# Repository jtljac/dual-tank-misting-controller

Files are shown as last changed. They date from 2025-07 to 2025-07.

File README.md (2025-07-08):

A circuit board design and ESPHome script for a control board responsible for a misting system for two tanks.  
A route from the pump to each tank can be enabled using solenoids attched to their labelled terminals. Powered terminals
will be indicated by an indicator LED, including when the pump is powered.

There are also a header for a Dallas 1-Wire DS18b20 waterproof temperature sensor for measuring the temperature of the 
water Tank, and a header for a HC-SR04 ultrasonic Distance sensor for use as a water level indicator. The HC-SR04 header
has an associate voltage selector header as they're supposed to be 5v but my cheap ones overheated above 3v3.

The board is powered using a 24V DC Barrel Jack and powers the pump and solenoids directly. This design has sized 
components and traces for 3A, which is generous for the required current for the ESP, pump, and two solenoids.

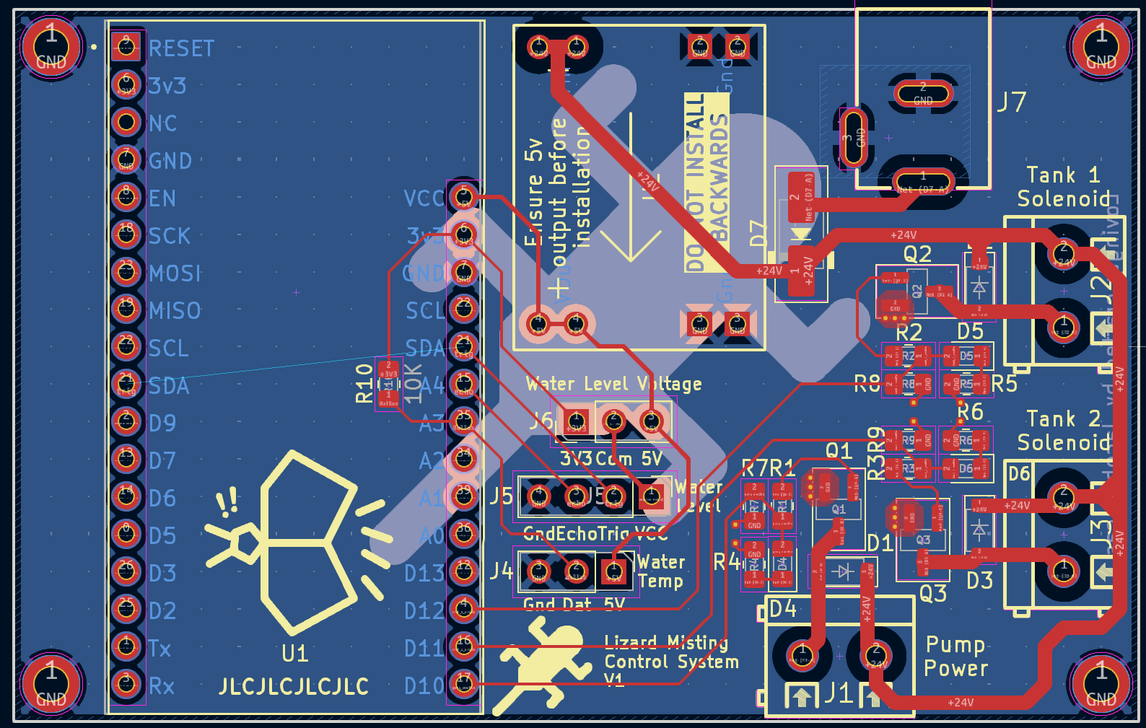
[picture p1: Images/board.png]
V1 Board


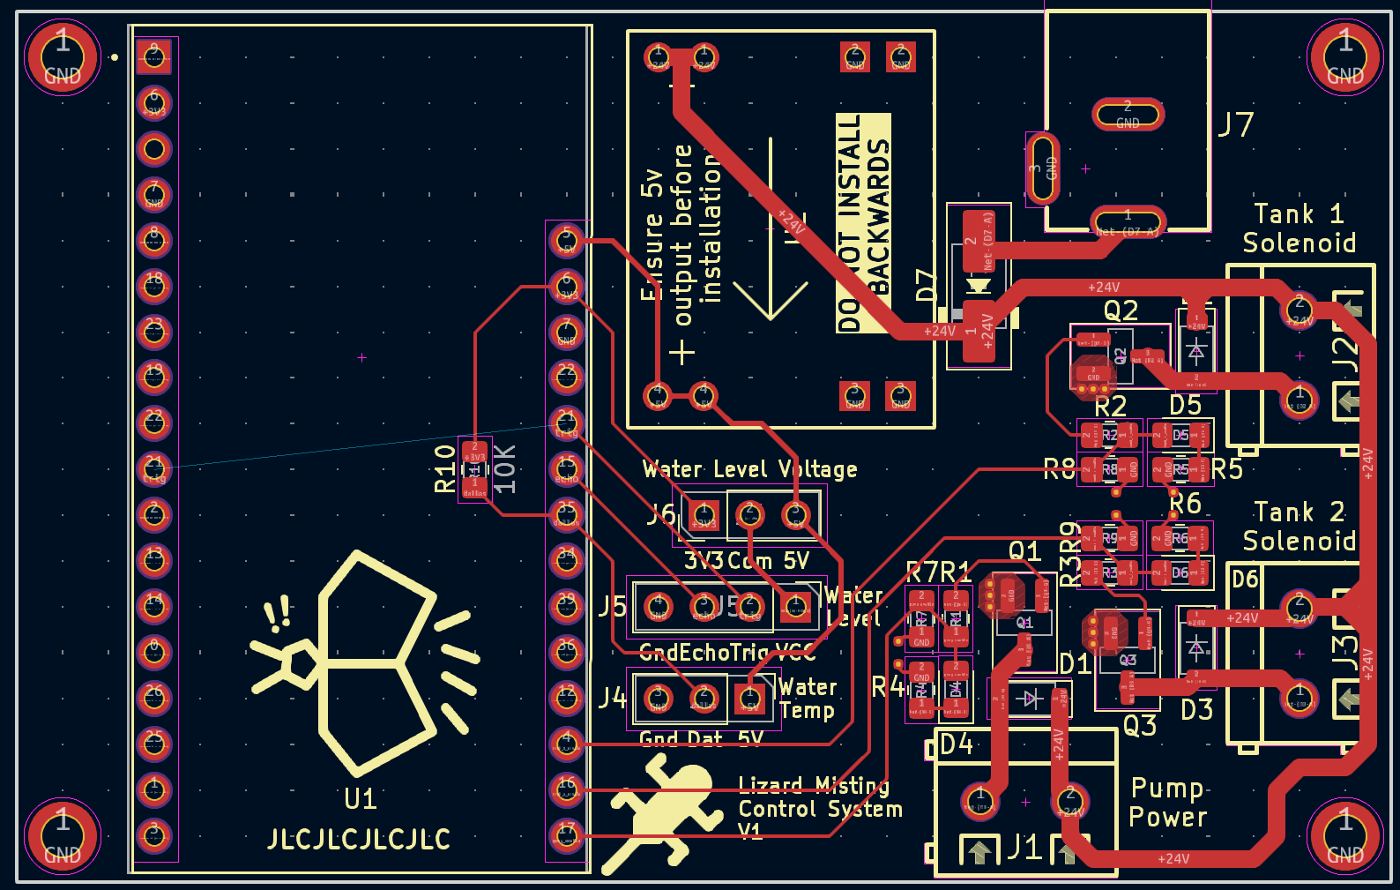
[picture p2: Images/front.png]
V1 Board Front Only


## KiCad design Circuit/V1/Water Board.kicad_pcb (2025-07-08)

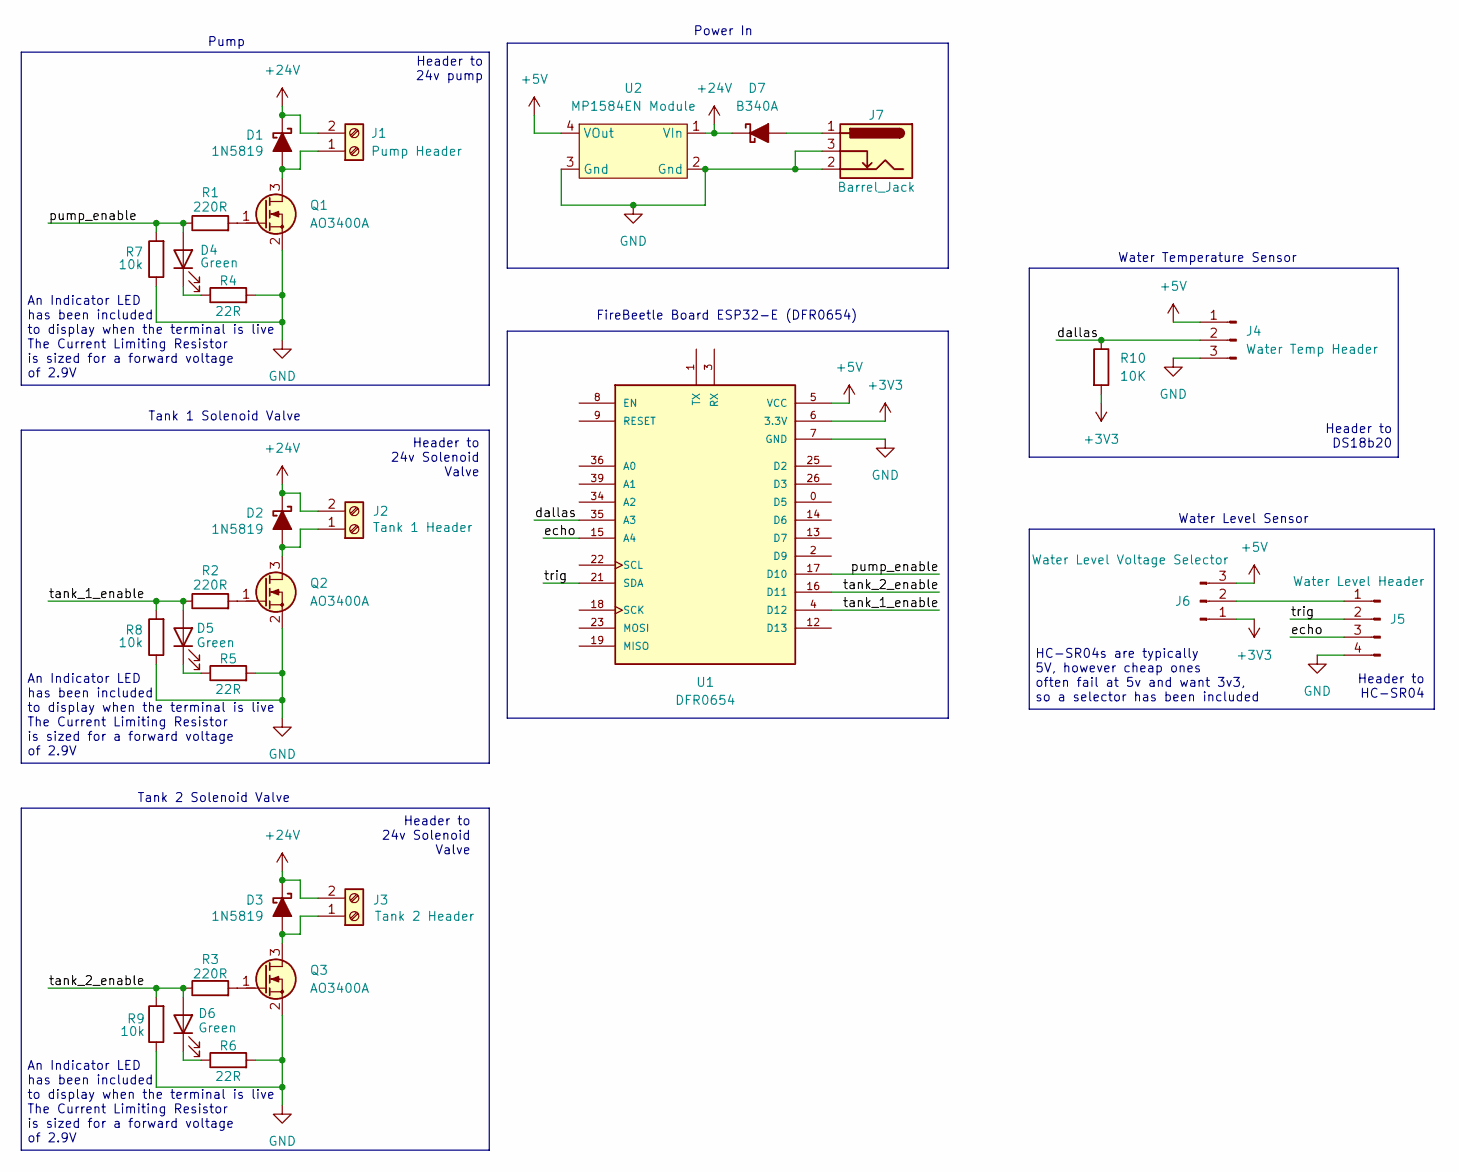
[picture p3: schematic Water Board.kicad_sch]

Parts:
D1, D2, D3: 1N5819; D_SOD-123
D4, D5, D6: Green; LED_0805_2012Metric_Pad1.15x1.40mm_HandSolder
D7: B340A; D_SMA_BigPads
J1: Pump Header; TerminalBlock_MAX_MX127-5.0-02P_1x02_P5.00mm
J2: Tank 1 Header; TerminalBlock_MAX_MX127-5.0-02P_1x02_P5.00mm
J3: Tank 2 Header; TerminalBlock_MAX_MX127-5.0-02P_1x02_P5.00mm
J4: Water Temp Header; PinHeader_1x03_P2.54mm_Vertical
J5: Water Level Header; PinHeader_1x04_P2.54mm_Vertical
J6: Water Level Voltage Selector; PinHeader_1x03_P2.54mm_Vertical
J7: Barrel_Jack; BarrelJack_XKB_5A
Q1, Q2, Q3: AO3400A; SOT-23_BigPads
R1, R2, R3: 220R; R_0805_2012Metric_Pad1.20x1.40mm_HandSolder
R4, R5, R6: 22R; R_0805_2012Metric_Pad1.20x1.40mm_HandSolder
R7, R8, R9: 10k; R_0805_2012Metric_Pad1.20x1.40mm_HandSolder
R10: 10K; R_0805_2012Metric_Pad1.20x1.40mm_HandSolder
U1: DFR0654; MODULE_DFR0654
U2: MP1584EN Module

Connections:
+3V3: J6.1, R10.2, U1.6 (3.3V)
+5V: J4.1, J6.3, U1.5 (VCC), U2.4 (VOut)
+24V: D1.1 (K), D2.1 (K), D3.1 (K), D7.1 (K), J1.2, J2.2, J3.2, U2.1 (VIn)
/dallas: J4.2, R10.1, U1.35 (A3)
/echo: J5.3, U1.15 (A4)
/pump_enable: D4.2 (A), R1.1, R7.2, U1.17 (D10)
/tank_1_enable: D5.2 (A), R2.1, R8.2, U1.4 (D12)
/tank_2_enable: D6.2 (A), R3.1, R9.2, U1.16 (D11)
/trig: J5.2, U1.21 (SDA)
GND: J4.3, J5.4, J7.2, J7.3, Q1.2 (S), Q2.2 (S), Q3.2 (S), R4.2, R5.2, R6.2, R7.1, R8.1, R9.1, U1.7 (GND), U2.2 (Gnd), U2.3 (Gnd); also elsewhere on the board
unnamed: D1.2 (A), J1.1, Q1.3 (D)
unnamed: D2.2 (A), J2.1, Q2.3 (D)
unnamed: D3.2 (A), J3.1, Q3.3 (D)
unnamed: D4.1 (K), R4.1
unnamed: D5.1 (K), R5.1
unnamed: D6.1 (K), R6.1
unnamed: D7.2 (A), J7.1
unnamed: J5.1, J6.2
unnamed: Q1.1 (G), R1.2
unnamed: Q2.1 (G), R2.2
unnamed: Q3.1 (G), R3.2

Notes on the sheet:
Water Level Sensor
Tank 1 Solenoid Valve
Water Temperature Sensor
An Indicator LED has been included to display when the terminal is live The Current Limiting Resistor is sized for a forward voltage of 2.9V
FireBeetle Board ESP32-E (DFR0654)
Header to HC-SR04
Power In
Header to 24v Solenoid Valve
Tank 2 Solenoid Valve
Pump
HC-SR04s are typically 5V, however cheap ones often fail at 5v and want 3v3, so a selector has been included
Header to DS18b20
Header to 24v pump

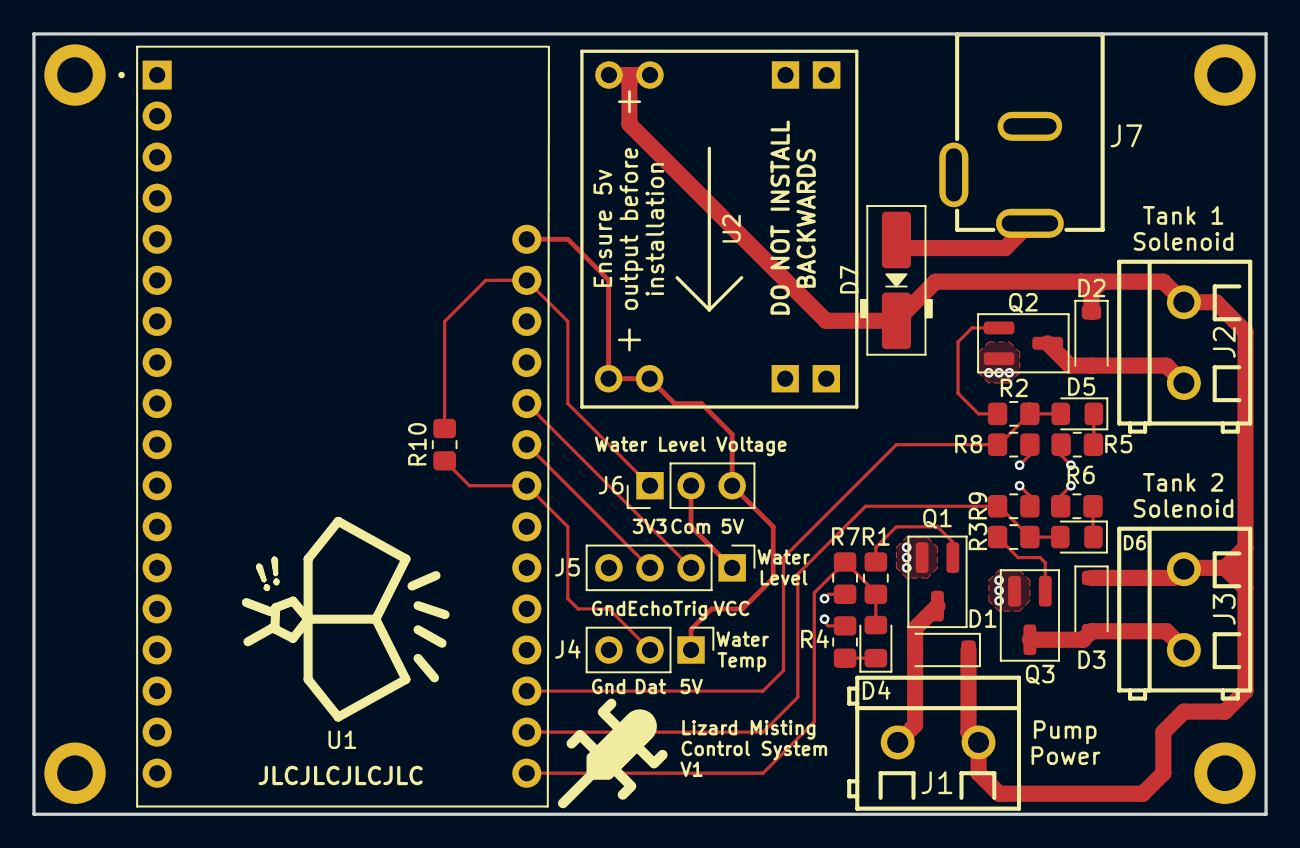
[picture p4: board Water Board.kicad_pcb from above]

Board: 2 copper layers, 76.2 x 48.3 mm, 33 parts (0 on the bottom side), 21 nets.

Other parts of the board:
M1, M2, M3, M4: MountingHole_2.2mm_M2_DIN965_Pad

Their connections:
GND: M1.1, M2.1, M3.1, M4.1; also elsewhere on the board

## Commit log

2025-07-07 Added pull down resistors to mosfets
    [Water Board.kicad_pcb, Water Board.kicad_sch]
2025-07-08 Revise resistor and LED layout, Added preview images
    [Water Board.kicad_pcb]
